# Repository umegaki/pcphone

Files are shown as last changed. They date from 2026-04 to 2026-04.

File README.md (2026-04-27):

# PCPhone とは
* PC Phone is a telephone assist device for physical disabilities. 
* PCホンは、肢体不自由のために固定電話機の操作ができない人が、PCから固定電話を操作できるようにするデバイスです。
* 原則として、オープンハードウェアとして公開していますが、ライセンス条件は、まだ書きかけです。変更される可能性があります。

# 構成

次の3つで構成されます。

1. 固定電話機（要改造）
2. PcPhone Arduino コントローラ
3. PcPhone Windows アプリケーション

# 注意喚起

電話機とコントローラの接続には電話機の改造が必要になります。このような改造は、技術基準適合認定（*技適*）に違反することになります。特に、電波を発する機器の場合には、その運用はより厳しくなります。したがって、通信回線にかかわる部分を改造しない、無線を搭載した固定電話機を使用しない、直接電話回線網に接続せず ONUやルーターを介して接続する、という点に注意を払いました。しかし、改造それ自体は違法とされる可能性のある行為です。今回は、障害者が回線を使えなければ利用できないサービスがあることを前提にして、電気通信事業法の趣旨を尊重しつつ、障害者の情報アクセスの権利を確保するにはやむをえないと判断しました。本機のユーザは、サービスを利用できない旨を当該運営会社に連絡し対応策を求めました。当該企業の担当者はそのユーザを訪問し現状を把握しましたが、今のところ対応策はないという結論でした。その後、ユーザから作者に相談を持ち掛けられました。

サービスを提供する運営会社は、障害者がサービスを利用できない状態であることに対して苦情を申し立てているのですから、合理的配慮に基づいた対策をすべきであり、それが本来行われるべき対策です。本機の開発はそのようなサポート不在に対するやむを得ない解決策であったことも付け加えておきます。

また、作者は、アナログ第2種工事担当者資格（旧電話工事資格）を持っており、その責任において、回線網に影響を与えないよう十分に配慮して設計しました。

作者は、このように不法性を問われるリスクを冒すことを問題なしとは考えません。障害者に対する合理的配慮の欠如によって生じる問題であり、このようなデバイスは本来必要なものではないし、またその制作を推進する立場にもありません。ここで公開する情報を利用して何らかの機器開発を行うときには、ここで述べた事項について自身の責任において実施してください。

#  PcPhone Arduino コントローラ

PCからのコマンドを受け付けて、電話機のボタンを押すための制御部です。

* Arduino nano R3 を用いました。
* 電話機の0～9、#*、ハンズフリ－の各ボタンの配線を確認して、それらをリレーを用いてオンすることによって、電話をかけることができる構造です。
* PCとの通信は、Arduino の USB と統合された仮想シリアルポートを通じて行います。
* リレーの個数を節約するために、電話機のボタンをスキャンする信号 COL、ROW を個別にオンします。この仕様は、電話機のボタンのスキャン方式に依存します。
* 半導体スイッチではなくメカニカルリレーを使用した理由は、できるだけ電話機本体と疎結合にすること、サージなどの影響を受けても発火・感電事故などが起きにくくするためです。
* 電話機との接続には、14ピンのフラットケーブルを使用していますが、ケーブルやボックスヘッダーが秋月電子通商で安価に購入できることが理由です。
* タカチ電機工業 LC型ハンドタイププラスチックケース(オフホワイト) LC135H-N-W に収まるようにJLCPCBでプリント基板を製造しました。
  
pc-phone hardware

# PcPhone Windows アプリケーション

* USB 仮想シリアルポートを介して、コントローラにコマンド文字を送信することで、電話機を操作します。

pc-phone-winapp-s

# 固定電話機

* シンプルシニアホン ブラック_TEL-2991SO-K 05-2991 （オーム電機）を使用しました。 [https://www.ohm-electric.co.jp/product/c17/c1704/37945/]
* 国産で、技適があり、アダプタ不要で回線だけで動作する、ハンズフリー機能のあるものを選択しました。
* この電話機の制御には、Silan Semiconductor 社の SC91415 が使用されています。
* ここにデータシートがあります。[https://www.digchip.com/datasheets/parts/datasheet/433/SC91415-pdf.php]

# ファイルの説明

* Pc-Phone.kicad_pcb KiCADの基板データ
* PcPhone.kicad_sch KiCADの回路図、PcPhone_sch.pdf 回路図のPDF
* PcPhoneBOM.csv 部品表
* pcphone-arduino.ino Arduinoプログラムソースコード

基板データは、Arduino D0 D1 を D12 D11 に変更する前のものです。そのまま使用するときは、基板のパターン2本をカットして、ジャンパーで修正する必要があります。
Windowsアプリケーションのソースコードは、準備できましたら公開します。

# 作者について
* この公開情報は、[https://github.com/umegaki/pcphone/] です。
* 作者のサイトは、[https://www.umegaki.jp/] です。

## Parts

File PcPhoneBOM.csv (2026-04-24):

Reference | Qty | Value | Footprint | Datasheet
A1 | 1 | ‎Hailege ‎H-A-1714 | Module:Arduino_Nano | http://www.mouser.com/pdfdocs/Gravitech_Arduino_Nano3_0.pdf
C1 | 1 | 0.1 | Capacitor_THT:C_Disc_D3.0mm_W1.6mm_P2.50mm | ~
C2,C4 | 2 | 47uF | Capacitor_THT:CP_Radial_D8.0mm_P3.80mm | ~
C3 | 1 | 100uF | Capacitor_THT:CP_Radial_D8.0mm_P3.80mm | ~
D1,D2,D3,D4,D5,D6,D7,D8,D11 | 9 | LED | LED_THT:LED_D3.0mm | ~
J1,J10 | 2 | Conn_02x07_Odd_Even | Connector_IDC:IDC-Header_2x07_P2.54mm_Horizontal | ~
J3 | 1 | Conn_01x02 | Connector_PinHeader_2.54mm:PinHeader_1x02_P2.54mm_Vertical | ~
J11 | 1 | Conn_02x07_Odd_Even | Connector_IDC:IDC-Header_2x07_P2.54mm_Vertical | ~
K1,K2,K3,K4,K5,K6,K7,K8 | 8 | G5V-2(compatible) | Relay_THT:Relay_DPDT_Omron_G5V-2 | http://omronfs.omron.com/en_US/ecb/products/pdf/en-g5v_2.pdf
Q11 | 1 | 2SC1815 | Package_TO_SOT_THT:TO-92_Inline | https://media.digikey.com/pdf/Data%20Sheets/Toshiba%20PDFs/2SC1815.pdf
R1,R2,R3,R4,R5,R6,R7,R8,R12 | 9 | 1K | Resistor_THT:R_Axial_DIN0207_L6.3mm_D2.5mm_P5.08mm_Vertical | ~
R9,R13,R14,R15,R16 | 5 | 1 | Resistor_THT:R_Axial_DIN0207_L6.3mm_D2.5mm_P5.08mm_Vertical | ~
R10,R11 | 2 | 10K | Resistor_THT:R_Axial_DIN0207_L6.3mm_D2.5mm_P5.08mm_Vertical | ~
RN1 | 1 | 10Kx8 | Resistor_THT:R_Array_SIP9 | http://www.vishay.com/docs/31509/csc.pdf
U1 | 1 | TD62083AFG | Package_DIP:DIP-18_W7.62mm | http://www.promelec.ru/pdf/1536.pdf
U2 | 1 | LM7805_TO220 | Package_TO_SOT_THT:TO-220-3_Vertical | https://www.onsemi.cn/PowerSolutions/document/MC7800-D.PDF

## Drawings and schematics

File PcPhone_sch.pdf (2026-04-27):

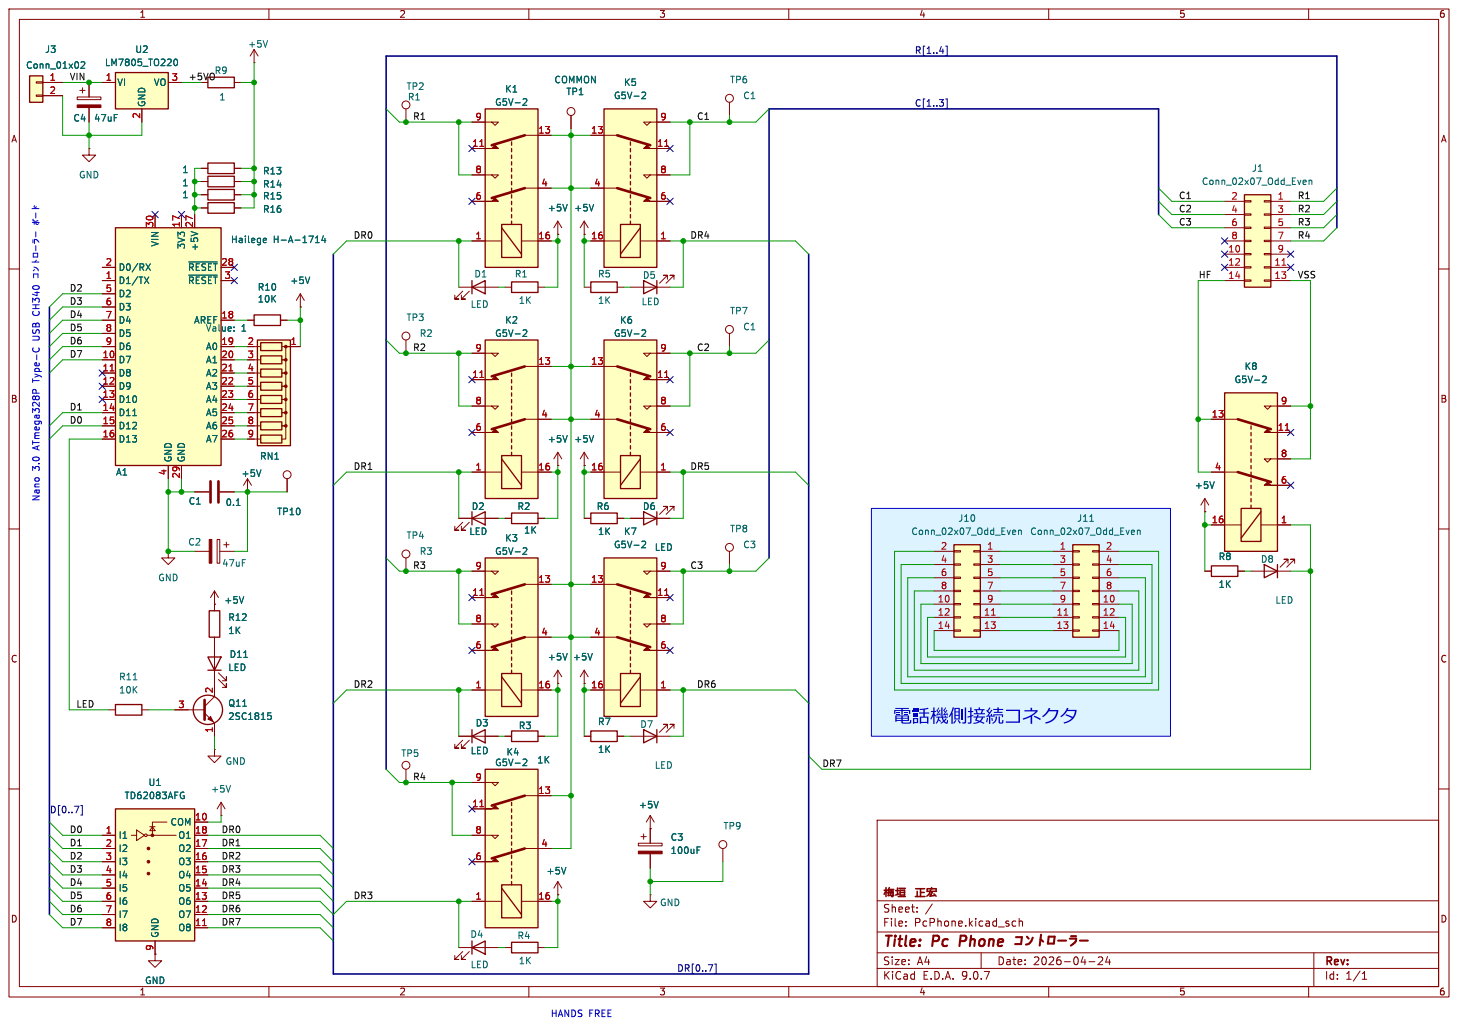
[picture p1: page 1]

Id: 1/1 Title: Pc Phone þÿ0³0ó0È0í0ü0é0ü

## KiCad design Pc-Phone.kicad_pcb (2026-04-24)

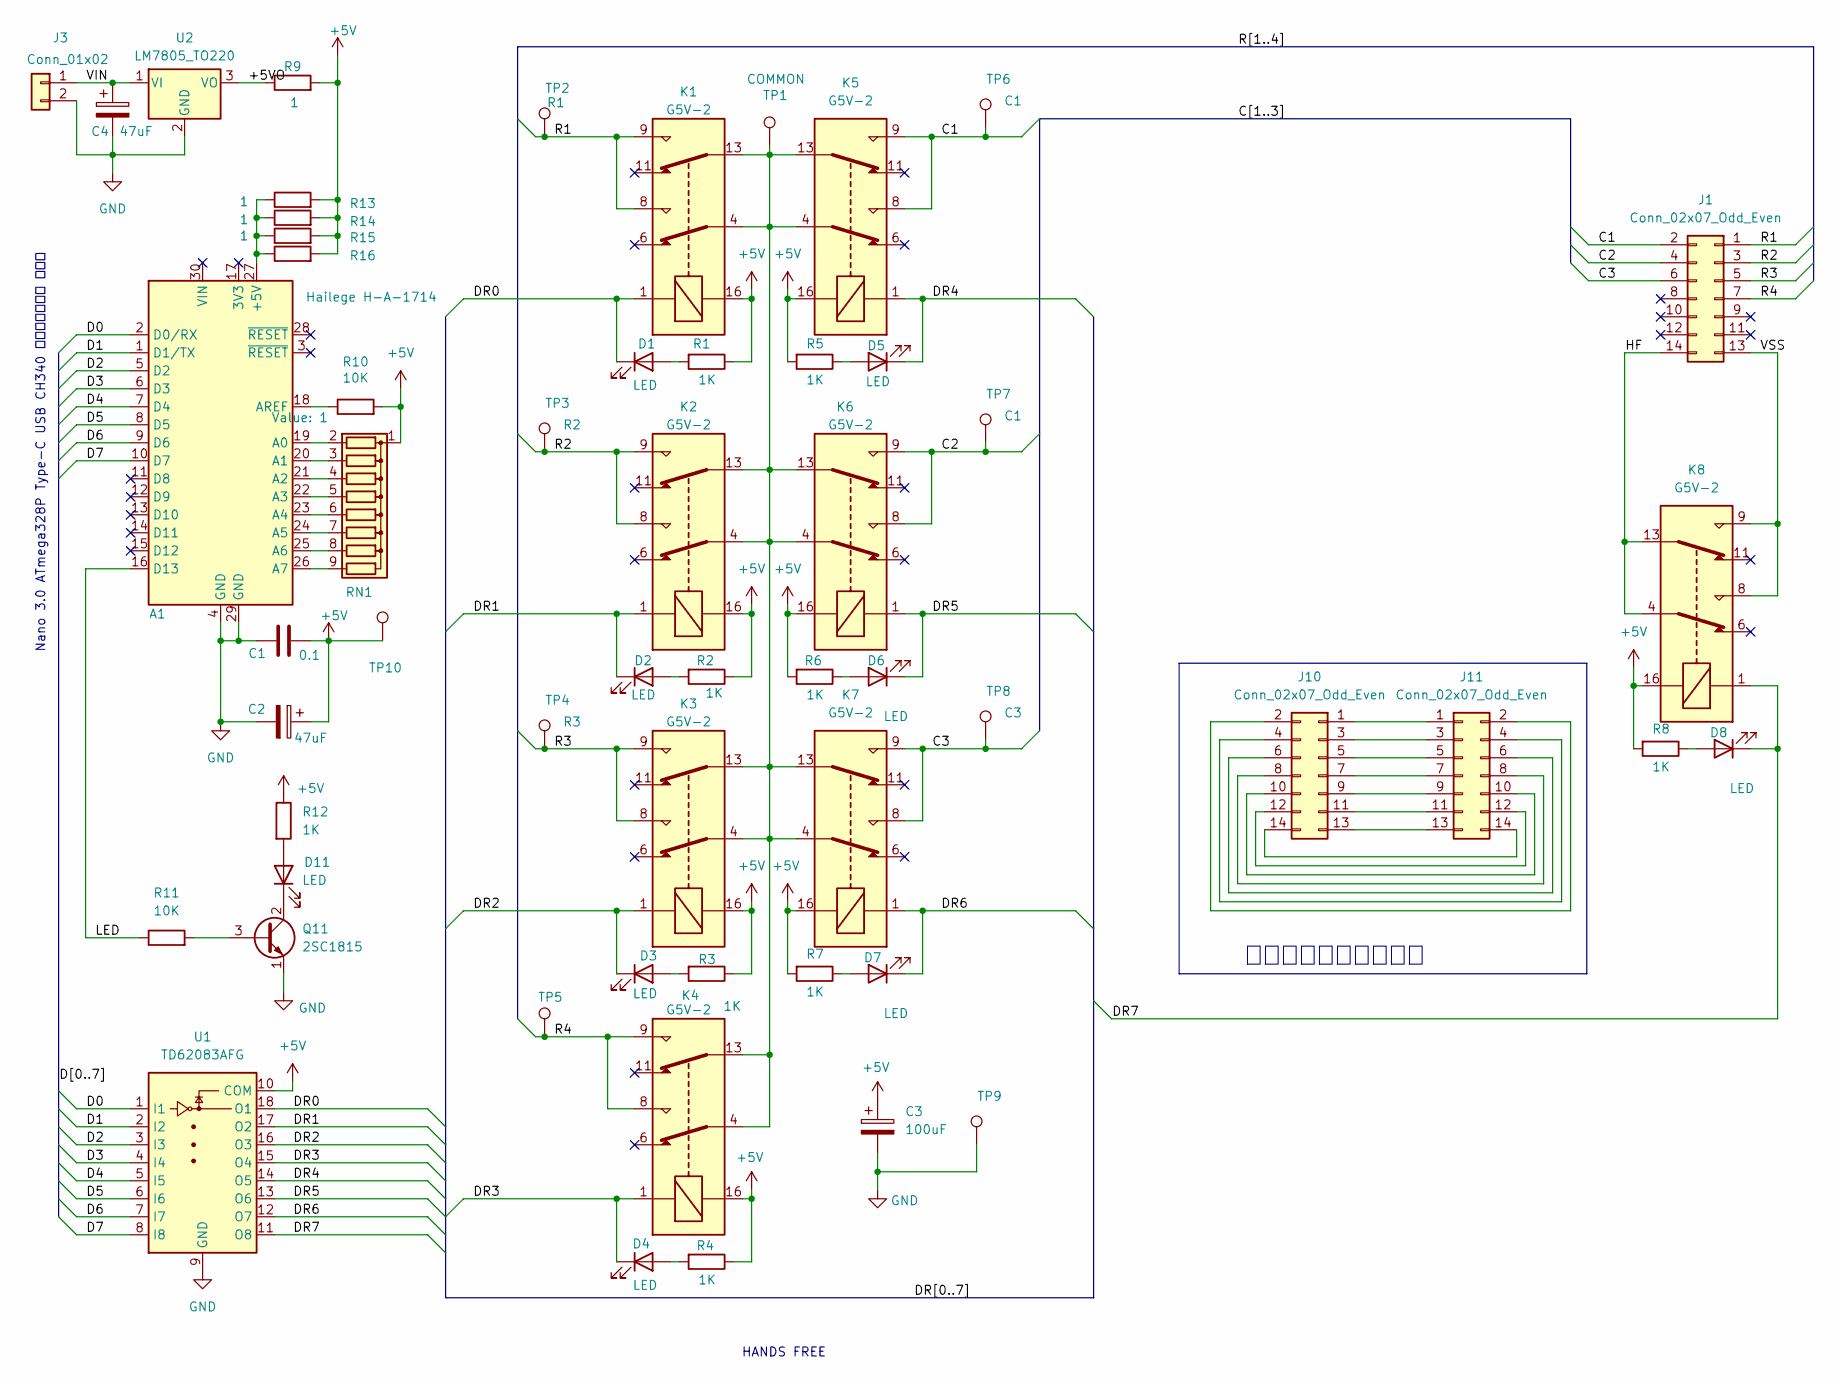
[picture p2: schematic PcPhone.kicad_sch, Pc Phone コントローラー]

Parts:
A1: ‎Hailege ‎H-A-1714; Arduino_Nano
C1: 0.1; C_Disc_D3.0mm_W1.6mm_P2.50mm
C2, C4: 47uF; CP_Radial_D8.0mm_P3.80mm
C3: 100uF; CP_Radial_D8.0mm_P3.80mm
D1, D2, D3, D4, D5, D6, D7, D8, D11: LED; LED_D3.0mm
J1, J10: Conn_02x07_Odd_Even; IDC-Header_2x07_P2.54mm_Horizontal
J3: Conn_01x02; PinHeader_1x02_P2.54mm_Vertical
J11: Conn_02x07_Odd_Even; IDC-Header_2x07_P2.54mm_Vertical
K1, K2, K3, K4, K5, K6, K7, K8: G5V-2; Relay_DPDT_Omron_G5V-2
Q11: 2SC1815; TO-92_Inline
R1, R2, R3, R4, R5, R6, R7, R8, R12: 1K; R_Axial_DIN0207_L6.3mm_D2.5mm_P5.08mm_Vertical
R9, R13, R14, R15, R16: 1; R_Axial_DIN0207_L6.3mm_D2.5mm_P5.08mm_Vertical
R10, R11: 10K; R_Axial_DIN0207_L6.3mm_D2.5mm_P5.08mm_Vertical
RN1: R_Network08; R_Array_SIP9
TP1: COMMON; Pin_D1.0mm_L10.0mm
TP2: R1; Pin_D1.0mm_L10.0mm
TP3: R2; Pin_D1.0mm_L10.0mm
TP4, TP9, TP10: R3; Pin_D1.0mm_L10.0mm
TP5: R4; Pin_D1.0mm_L10.0mm
TP6, TP7: C1; Pin_D1.0mm_L10.0mm
TP8: C3; Pin_D1.0mm_L10.0mm
U1: TD62083AFG; DIP-18_W7.62mm
U2: LM7805_TO220; TO-220-3_Vertical

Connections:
+5V: C1.1, C2.1, C3.1, K1.16, K2.16, K3.16, K4.16, K5.16, K6.16, K7.16, K8.16, R1.1, R2.1, R3.1, R4.1, R5.2, R6.2, R7.2, R8.2, R9.2, R10.2, R12.1, R13.2, R14.2, R15.2, R16.2, RN1.1 (common), TP10.1, U1.10 (COM)
/+5VO: R9.1, U2.3 (VO)
/C1: J1.2, K5.8, K5.9, TP6.1
/C2: J1.4, K6.8, K6.9, TP7.1
/C3: J1.6, K7.8, K7.9, TP8.1
/D0: A1.2 (D0/RX), U1.1 (I1)
/D1: A1.1 (D1/TX), U1.2 (I2)
/D2: A1.5 (D2), U1.3 (I3)
/D3: A1.6 (D3), U1.4 (I4)
/D4: A1.7 (D4), U1.5 (I5)
/D5: A1.8 (D5), U1.6 (I6)
/D6: A1.9 (D6), U1.7 (I7)
/D7: A1.10 (D7), U1.8 (I8)
/DR0: D1.1 (K), K1.1, U1.18 (O1)
/DR1: D2.1 (K), K2.1, U1.17 (O2)
/DR2: D3.1 (K), K3.1, U1.16 (O3)
/DR3: D4.1 (K), K4.1, U1.15 (O4)
/DR4: D5.1 (K), K5.1, U1.14 (O5)
/DR5: D6.1 (K), K6.1, U1.13 (O6)
/DR6: D7.1 (K), K7.1, U1.12 (O7)
/DR7: D8.1 (K), K8.1, U1.11 (O8)
/HF: J1.14, K8.4, K8.13
/LED: A1.16 (D13), R11.1
/R1: J1.1, K1.8, K1.9, TP2.1
/R2: J1.3, K2.8, K2.9, TP3.1
/R3: J1.5, K3.8, K3.9, TP4.1
/R4: J1.7, K4.8, K4.9, TP5.1
/VIN: C4.1, J3.1, U2.1 (VI)
/VSS: J1.13, K8.8, K8.9
GND: A1.4 (GND), A1.29 (GND), C1.2, C2.2, C3.2, C4.2, J3.2, Q11.1 (E), TP9.1, U1.9 (GND), U2.2 (GND)
unnamed: A1.27 (+5V), R13.1, R14.1, R15.1, R16.1
unnamed: A1.19 (A0), RN1.2 (R1)
unnamed: A1.20 (A1), RN1.3 (R2)
unnamed: A1.21 (A2), RN1.4 (R3)
unnamed: A1.22 (A3), RN1.5 (R4)
unnamed: A1.23 (A4), RN1.6 (R5)
unnamed: A1.24 (A5), RN1.7 (R6)
unnamed: A1.25 (A6), RN1.8 (R7)
unnamed: A1.26 (A7), RN1.9 (R8)
unnamed: A1.18 (AREF), R10.1
unnamed: D1.2 (A), R1.2
unnamed: D2.2 (A), R2.2
unnamed: D3.2 (A), R3.2
unnamed: D4.2 (A), R4.2
unnamed: D5.2 (A), R5.1
unnamed: D6.2 (A), R6.1
unnamed: D7.2 (A), R7.1
unnamed: D8.2 (A), R8.1
unnamed: D11.2 (A), R12.2
unnamed: D11.1 (K), Q11.2 (C)
unnamed: J10.1, J11.1
unnamed: J10.2, J11.2
unnamed: J10.3, J11.3
unnamed: J10.4, J11.4
unnamed: J10.5, J11.5
unnamed: J10.6, J11.6
unnamed: J10.7, J11.7
unnamed: J10.8, J11.8
unnamed: J10.9, J11.9
unnamed: J10.10, J11.10
unnamed: J10.11, J11.11
unnamed: J10.12, J11.12
unnamed: J10.13, J11.13
unnamed: J10.14, J11.14
unnamed: K1.4, K1.13, K2.4, K2.13, K3.4, K3.13, K4.4, K4.13, K5.4, K5.13, K6.4, K6.13, K7.4, K7.13, TP1.1
unnamed: Q11.3 (B), R11.2

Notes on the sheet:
電話機側接続コネクタ
HANDS FREE
Nano 3.0 ATmega328P Type-C USB CH340 コントローラー ボード

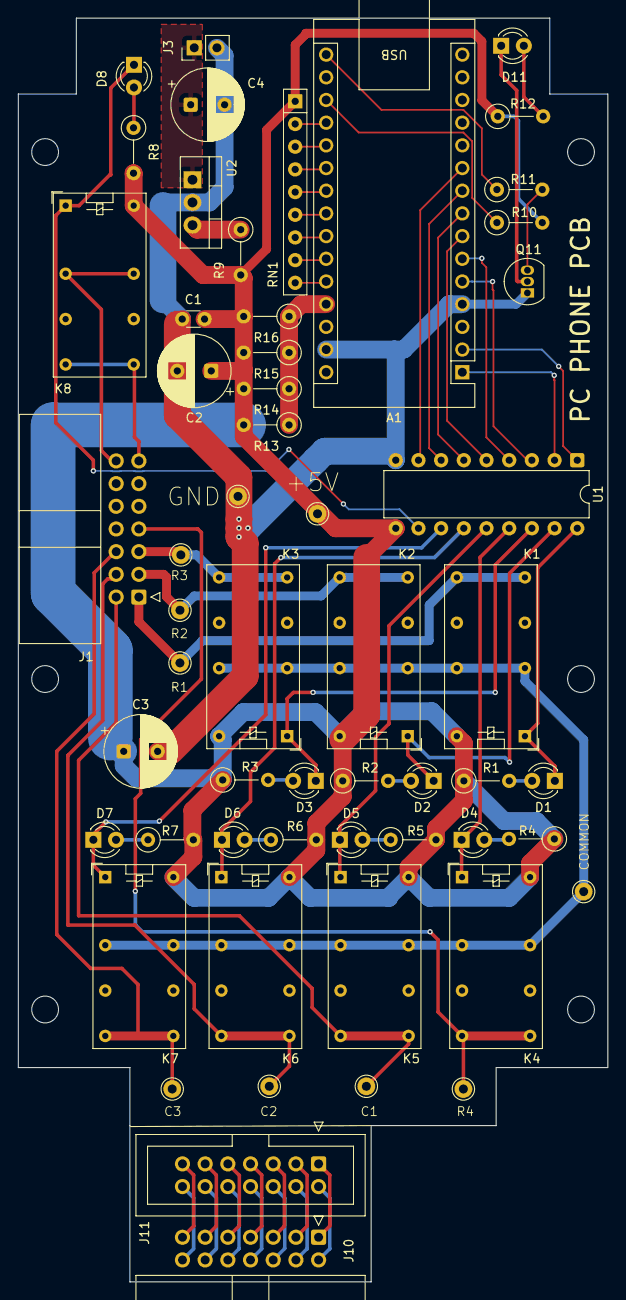
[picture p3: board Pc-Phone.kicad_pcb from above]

Board: 2 copper layers, 66.0 x 141.5 mm, 56 parts (0 on the bottom side), 66 nets.

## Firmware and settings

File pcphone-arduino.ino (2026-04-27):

// PC Phone コントローラ
// arduino nano r3
// M.Umegaki 2025-12-11 (birthday)

#define PUSH_TIME 250    // 番号ボタンを押す時間
#define RELEASE_TIME 250  // 番号ボタンを押した後の休止時間
#define WAIT_TIME 1000

#define POWER_LED 13
#define DR0 12
#define DR1 11
#define DR2 2
#define DR3 3
#define DR4 4
#define DR5 5
#define DR6 6
#define DR7 7

#define C1 4
#define C2 5
#define C3 6

#define R1 12
#define R2 11
#define R3 2
#define R4 3

/* definition DR[0..7] */
const unsigned int DR_PORT[8] = { DR0, DR1, DR2, DR3, DR4, DR5, DR6, DR7 };

#define HANDS_FREE 7

/* definition 2 relay ports to push button*/

const unsigned int BUTTON_0_CR[2] = { C2, R4 };     /* 0 C2 R2 */
const unsigned int BUTTON_1_CR[2] = { C1, R1 };     /* 1 C1 R1 */
const unsigned int BUTTON_2_CR[2] = { C2, R1 };     /* 2 C2 R1 */
const unsigned int BUTTON_3_CR[2] = { C3, R1 };     /* 3 C3 R1 */
const unsigned int BUTTON_4_CR[2] = { C1, R2 };     /* 4 C1 R2 */
const unsigned int BUTTON_5_CR[2] = { C2, R2 };     /* 5 C2 R2 */
const unsigned int BUTTON_6_CR[2] = { C3, R2 };     /* 6 C3 R2 */
const unsigned int BUTTON_7_CR[2] = { C1, R3 };     /* 7 C1 R3 */
const unsigned int BUTTON_8_CR[2] = { C2, R3 };     /* 8 C2 R3 */
const unsigned int BUTTON_9_CR[2] = { C3, R3 };     /* 9 C3 R3 */
const unsigned int BUTTON_ASTERISK_CR[2] = { C1, R4 }; /* "*" C1 R4 */
const unsigned int BUTTON_SHARP_CR[2] = { C3, R4 };    /* "#" C1 R4 */

// 初期化
void setup() {
  PORTB = 0x00;
  PORTD = 0x00;
  DDRD = B11111100;  // D0-D7
  DDRB = B11100000;  // D8-D13
  // pinMode(POWER_LED, OUTPUT);
  digitalWrite(POWER_LED, HIGH);
  Serial.begin(9600);  // Initialize serial communication at 9600 baud
  Serial.println("ready\n");
}

// メインループ
void loop() {
  if (Serial.available() > 0) sread();
}

// シリアル受信
void sread() {
    char data = Serial.read();
    Serial.print(data);
    switch (data) {
      case '0':
        push_button(BUTTON_0_CR);
        break;
      case '1':
        push_button(BUTTON_1_CR);
        break;
      case '2':
        push_button(BUTTON_2_CR);
        break;
      case '3':
        push_button(BUTTON_3_CR);
        break;
      case '4':
        push_button(BUTTON_4_CR);
        break;
      case '5':
        push_button(BUTTON_5_CR);
        break;
      case '6':
        push_button(BUTTON_6_CR);
        break;
      case '7':
        push_button(BUTTON_7_CR);
        break;
      case '8':
        push_button(BUTTON_8_CR);
        break;
      case '9':
        push_button(BUTTON_9_CR);
        break;
      case '#':
        push_button(BUTTON_SHARP_CR);
        break;
      case '*':
        push_button(BUTTON_ASTERISK_CR);
        break;
      case 'F':  // hand free on
      case 'f':  // hand free on
        hands_free(1);
        break;
      case 'G':  // hand free o
      case 'g':  // hand free o
        hands_free(0);
        break;
      case 'H':  // hand free o
      case 'h':  // hand free o
        hands_free(2);
        break;
      case 'T':
      case 't':
        port_test(1);
        break;
      case 'W':
      case 'w':
        wait1(1);
        break;
      case 'L':
      case 'l':
        wait1(10);
        break;

    }
}

void wait1(int c){
  if (c==1) {
    digitalWrite(POWER_LED, LOW);
    delay(WAIT_TIME);
    digitalWrite(POWER_LED, HIGH);
  } else {
    for (int i=0;i<c;i++) {
      digitalWrite(POWER_LED, LOW);
      delay(WAIT_TIME/2);
      digitalWrite(POWER_LED, HIGH);
      delay(WAIT_TIME/2);
    }
  }
}
// test circult
void port_test(int count) {
  Serial.println(" port test start");
  for (int c = 0; c < count; c++) {
    for (int i = 0; i < 8; i++) {
      digitalWrite(DR_PORT[i], HIGH);
      digitalWrite(POWER_LED, LOW);
      delay(1000);
      digitalWrite(DR_PORT[i], LOW);
      digitalWrite(POWER_LED, HIGH);
      delay(1000);
    }
  }
   Serial.println("port test end");
}

// hands free
void hands_free(int on) {
  if (on == 2) {
    digitalWrite(HANDS_FREE, HIGH);
    delay(PUSH_TIME);
    digitalWrite(HANDS_FREE, LOW);
    delay(RELEASE_TIME);
  } else if (on == 1) {
    digitalWrite(HANDS_FREE, HIGH);
    delay(PUSH_TIME);
  } else {
    digitalWrite(HANDS_FREE, LOW);
    delay(RELEASE_TIME);
  }
}

// push the button
void push_button(unsigned int *port_cr) {
  digitalWrite(port_cr[0], HIGH);
  digitalWrite(port_cr[1], HIGH);
  delay(PUSH_TIME);
  digitalWrite(port_cr[0], LOW);
  digitalWrite(port_cr[1], LOW);
  delay(RELEASE_TIME);
}

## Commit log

2026-04-24 Add files via upload
    KiCAD 回路図
    [PcPhone.kicad_sch]
2026-04-24 Add files via upload
    KiCAD PCB 設計データ
    [Pc-Phone.kicad_pcb]
2026-04-24 Update BOM entries in PcPhoneBOM.csv
    Replaced the existing BOM entries with updated values while maintaining the same structure.
    [PcPhoneBOM.csv]
